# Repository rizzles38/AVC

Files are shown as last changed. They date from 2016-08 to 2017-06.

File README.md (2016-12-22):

# Rover 12

An autonomous 1/10th scale R/C car built by Maria Pikusova and Bob Somers.

## Documentation

### Nodes

* `joint_state_publisher` (joint\_state\_publisher/joint\_state\_publisher):
  Listens on individual joint topics under `/joints` and  publishes a single
  sensor\_msgs/JointState which contains the state of all joints in the robot
  (based on the URDF).
* `robot_state_publisher` (robot\_state\_publisher/state\_publisher): Listens
  to the combined joint states of the robot on `/joint_states`, runs forward
  kinematics based on the URDF, and publishes the results to the TF2 tree.
* `control_board` (rover12\_drivers/control\_board\_node): Driver node which
  talks to the control board. Subscribes to the `/control/autonomous` and
  `/control/command` topics for controlling whether we're in autonomous mode and
  what the velocity/steering command is. Publishes data and status of the wheel
  encoders on the `/wheels/data` and `/wheels/status` topics, as well as the
  status of autonomous mode (from the control board) on `/estop`.
* `sensor_board` (rover12\_drivers/sensor\_board\_node): Publishes data from the
  IMU sensor and GPS sensor, including status information from both sensors
  about their operating modes, current performance, and calibration status.
* `soft_estop` (soft\_estop/soft\_estop): Continuously publishes on the
  `/control/autonomous` topic that requests that the hardware allow the robot to
  be in autonomous mode. Can be run on a computer different than the robot to
  have remote control of autonomous mode. Stands for "software emergency stop".
* `odom_localizer` (robot\_localization/ukf\_localization\_node): Runs an
  unscented Kalman filter over the wheel odometry and IMU data to produce a
  state estimate of `base_link` in the `odom` frame. Subscribes to `/imu/data`
  and `/wheels/data` for sensor inputs and publishes its pose estimate on
  `/odom/filtered`. Also publishes the transform from the `odom` frame to the
  `base_link` frame in the TF2 tree.

### Topics

* `/control`: Namespace for talking to the control board.
  * `/autonomous` (rover12\_drivers/AutonomousMode): Controls whether the
    software wants to be in autonomous mode or not.
  * `/command` (ackermann\_msgs/AckermannDriveStamped): Contains the velocity
    and steering angle command we want the car to execute.
* `/estop` (rover12\_drivers/AutonomousMode): The current state of autonomous
  mode, according to the control board. The firmware makes the final call, based
  on whether the software and physical autonomous mode switch are engaged.
* `/gps`: Namespace for the GPS sensor.
  * `/fix` (sensor\_msgs/NavSatFix): Current GPS position estimate.
  * `/status` (rover12\_drivers/GpsStatus): Extra status information from the
    GPS sensor.
* `/imu`: Namespace for the inertial sensor.
  * `/data` (sensor\_msgs/Imu): Current inertial data and absolute orientation
    estimate from the sensor.
  * `/status` (rover12\_drivers/ImuStatus): Extra status information from the
    IMU, such as its operating mode and calibration state.
* `/joint_states` (sensor\_msgs/JointState): A combined, consistent JointState
  for all joints in the robot, based on the URDF. Published by the
  `joint_state_publisher`.
* `/joints`: Namespace for controlling individual joint states.
  * `/fl_steer` (sensor\_msgs/JointState): Steering rotation of the front left kingpin.
  * `/fr_steer` (sensor\_msgs/JointState): Steering rotation of the front right kingpin.
  * `/fl_wheel` (sensor\_msgs/JointState): Rotation of the front left wheel.
  * `/fr_wheel` (sensor\_msgs/JointState): Rotation of the front right wheel.
  * `/rl_wheel` (sensor\_msgs/JointState): Rotation of the rear left wheel.
  * `/rr_wheel` (sensor\_msgs/JointState): Rotation of the rear right wheel.
* `/odom`: Namespace for pose information in the odom frame.
  * `/filtered` (nav\_msgs/Odometry): Output pose estimate from the UKF in the
    `odom` frame.
* `/wheels`: Namespace for the quadrature wheel encoders.
  * `/data` (geometry\_msgs/TwistWithCovarianceStamped): Instantaneous forward
    speed based on averaging wheel speeds from the quadrature wheel encoders.
  * `/status` (rover12\_drivers/EncoderStatus): Extra status data from the
    wheel encoders (such as raw tick counts).

### TF2 Frames
* `odom`: World-fixed frame in which `base_link` moves smoothly over the short
  term, but accumulates drift error over the long term. The origin of this frame
  is the startup location of the robot.
  * `base_link`: Fixed to robot, parent of all other frames attached to the
    robot. Origin is at the rear axle (X forward, Y out the driver's side, Z
    up).
    * `imu`: Origin at the sensing center of the IMU, oriented according to the
      IMUs local coordinate frame.
    * `gps`: Origen at the sensing center of the GPS antenna, oriented in the
      same direction as `base_link`.
    * `body`: Origin at the approximate center of mass of the body shell,
      primarily used for drawing the robot model at a sensible location in rviz.
    * `rl_wheel`: Origin in the center of the rear left wheel. Rotates about
      its Y axis as the wheel rotates. Located half the track distance from
      `base_link` along its Y axis.
    * `rr_wheel`: Origin in the center of the rear right wheel. Rotates about
      its Y axis as the wheel rotates. Located half the track distance from
      `base_link` along its Y axis.
    * `f_axle`: Origin in the center of the front axle, oriented in the same
      way as `base_link`. The distance between this frame and `base_link` is the
      wheelbase distance along their colinear X axes.
      * `fl_kingpin`: Origin in the steering center of the front left wheel,
        located half the track distance from `f_axle` along its Y axis. Rotates
        about its Z axis.
        * `fl_wheel`: Origin in the center of the front left wheel, orientation
          accounting for the rotation of `fl_kingpin`. Rotates about its Y axis
          as the wheel rotates.
      * `fr_kingpin`: Origin in the steering center of the front right wheel,
        located half the track distance from `f_axle` along its Y axis. Rotates
        about its Z axis.
        * `fr_wheel`: Origin in the center of the front right wheel, orientation
          accounting for the rotation of `fr_kingpin`. Rotates about its Y axis
          as the wheel rotates.

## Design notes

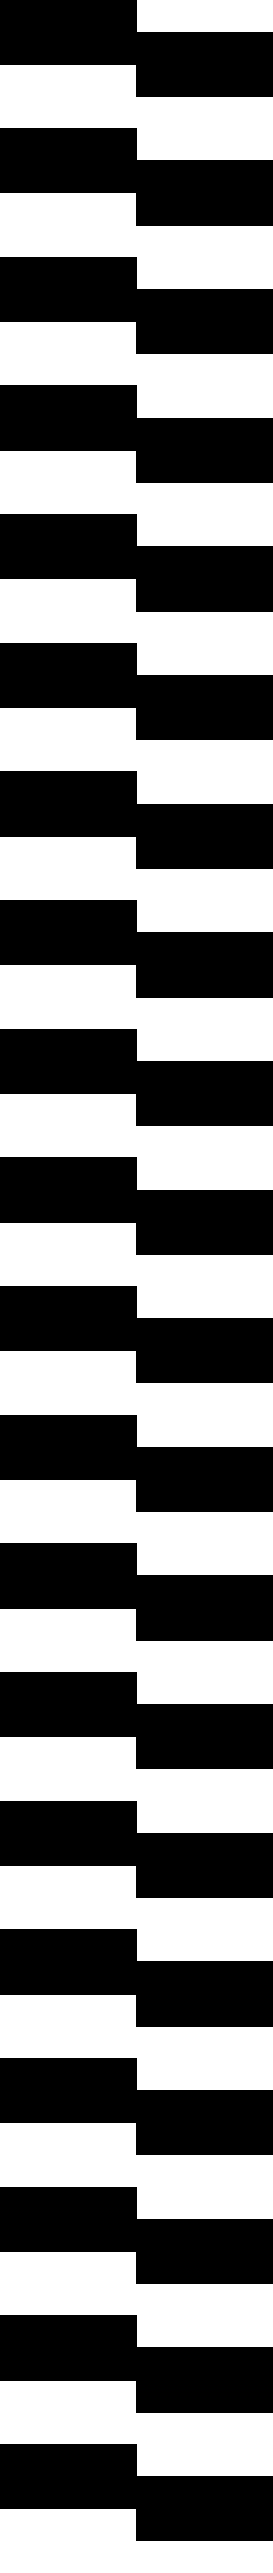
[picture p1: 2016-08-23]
tools/quadrature_patterns/pattern.png

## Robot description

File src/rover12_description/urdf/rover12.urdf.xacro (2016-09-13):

<?xml version="1.0"?>
<robot xmlns:xacro="http://www.ros.org/wiki/xacro" name="rover12">
  <xacro:property name="PI" value="3.1415926535897931"/>

  <xacro:property name="r_track" value="0.2667"/>
  <xacro:property name="f_track" value="0.257175"/>
  <xacro:property name="wheelbase" value="0.32385"/>

  <xacro:property name="wheel_width" value="0.0508"/>
  <xacro:property name="wheel_radius" value="0.0492125"/>

  <xacro:property name="gps_xyz" value="0.375 0 0.03"/>
  <xacro:property name="gps_rpy" value="0 0 0"/>

  <xacro:property name="imu_xyz" value="0.28 0.038 0.072"/>
  <xacro:property name="imu_rpy" value="0 0.0349066 1.55334"/>

  <material name="axle">
    <color rgba="1.0 1.0 1.0 1.0"/>
  </material>

  <xacro:macro name="axle" params="name track wheelbase">
    <link name="${name}">
      <visual>
        <geometry>
          <cylinder length="${track}" radius="0.00635"/>
        </geometry>
        <material name="axle"/>
        <origin rpy="${PI /2 } 0 0"/>
      </visual>
    </link>

    <joint name="base_link_to_${name}" type="fixed">
      <parent link="base_link"/>
      <child link="${name}"/>
      <origin xyz="${wheelbase} 0 0"/>
    </joint>
  </xacro:macro>

  <xacro:macro name="wheel" params="name reflect">
    <link name="${name}">
      <visual>
        <geometry>
          <mesh filename="package://rover12_description/meshes/wheel.dae" scale="0.5 ${reflect * 0.8} 0.5"/>
        </geometry>
      </visual>
    </link>
  </xacro:macro>

  <xacro:macro name="fixed_wheel" params="name axle track reflect">
    <xacro:wheel name="${name}_wheel" reflect="${reflect}"/>

    <joint name="${axle}_to_${name}_wheel" type="continuous">
      <parent link="${axle}"/>
      <child link="${name}_wheel"/>
      <axis xyz="0 1 0"/>
      <origin xyz="0 ${reflect * track / 2} 0"/>
    </joint>
  </xacro:macro>

  <xacro:macro name="steerable_wheel" params="name axle track reflect">
    <link name="${name}_kingpin"/>

    <joint name="${axle}_to_${name}_kingpin" type="continuous">
      <parent link="${axle}"/>
      <child link="${name}_kingpin"/>
      <axis xyz="0 0 1"/>
      <origin xyz="0 ${reflect * track / 2} 0"/>
    </joint>

    <xacro:fixed_wheel name="${name}" axle="${name}_kingpin" track="0" reflect="${reflect}"/>
  </xacro:macro>

  <link name="base_link">
    <visual>
      <geometry>
        <cylinder length="${r_track}" radius="0.00635"/>
      </geometry>
      <material name="axle"/>
      <origin rpy="${PI / 2} 0 0"/>
    </visual>
  </link>

  <xacro:fixed_wheel name="rl" axle="base_link" track="${r_track}" reflect="1"/>
  <xacro:fixed_wheel name="rr" axle="base_link" track="${r_track}" reflect="-1"/>

  <xacro:axle name="f_axle" track="${f_track}" wheelbase="${wheelbase}"/>

  <xacro:steerable_wheel name="fl" axle="f_axle" track="${f_track}" reflect="1"/>
  <xacro:steerable_wheel name="fr" axle="f_axle" track="${f_track}" reflect="-1"/>

  <link name="gps"/>

  <joint name="base_link_to_gps" type="fixed">
    <parent link="base_link"/>
    <child link="gps"/>
    <origin xyz="${gps_xyz}" rpy="${gps_rpy}"/>
  </joint>

  <link name="imu"/>

  <joint name="base_link_to_imu" type="fixed">
    <parent link="base_link"/>
    <child link="imu"/>
    <origin xyz="${imu_xyz}" rpy="${imu_rpy}"/>
  </joint>

  <link name="body">
    <visual>
      <geometry>
        <mesh filename="package://rover12_description/meshes/body.dae" scale="-0.48 0.5 0.5"/>
      </geometry>
    </visual>
  </link>

  <joint name="base_link_to_body" type="fixed">
    <parent link="base_link"/>
    <child link="body"/>
    <origin xyz="0.175 0 0.067"/>
  </joint>
</robot>

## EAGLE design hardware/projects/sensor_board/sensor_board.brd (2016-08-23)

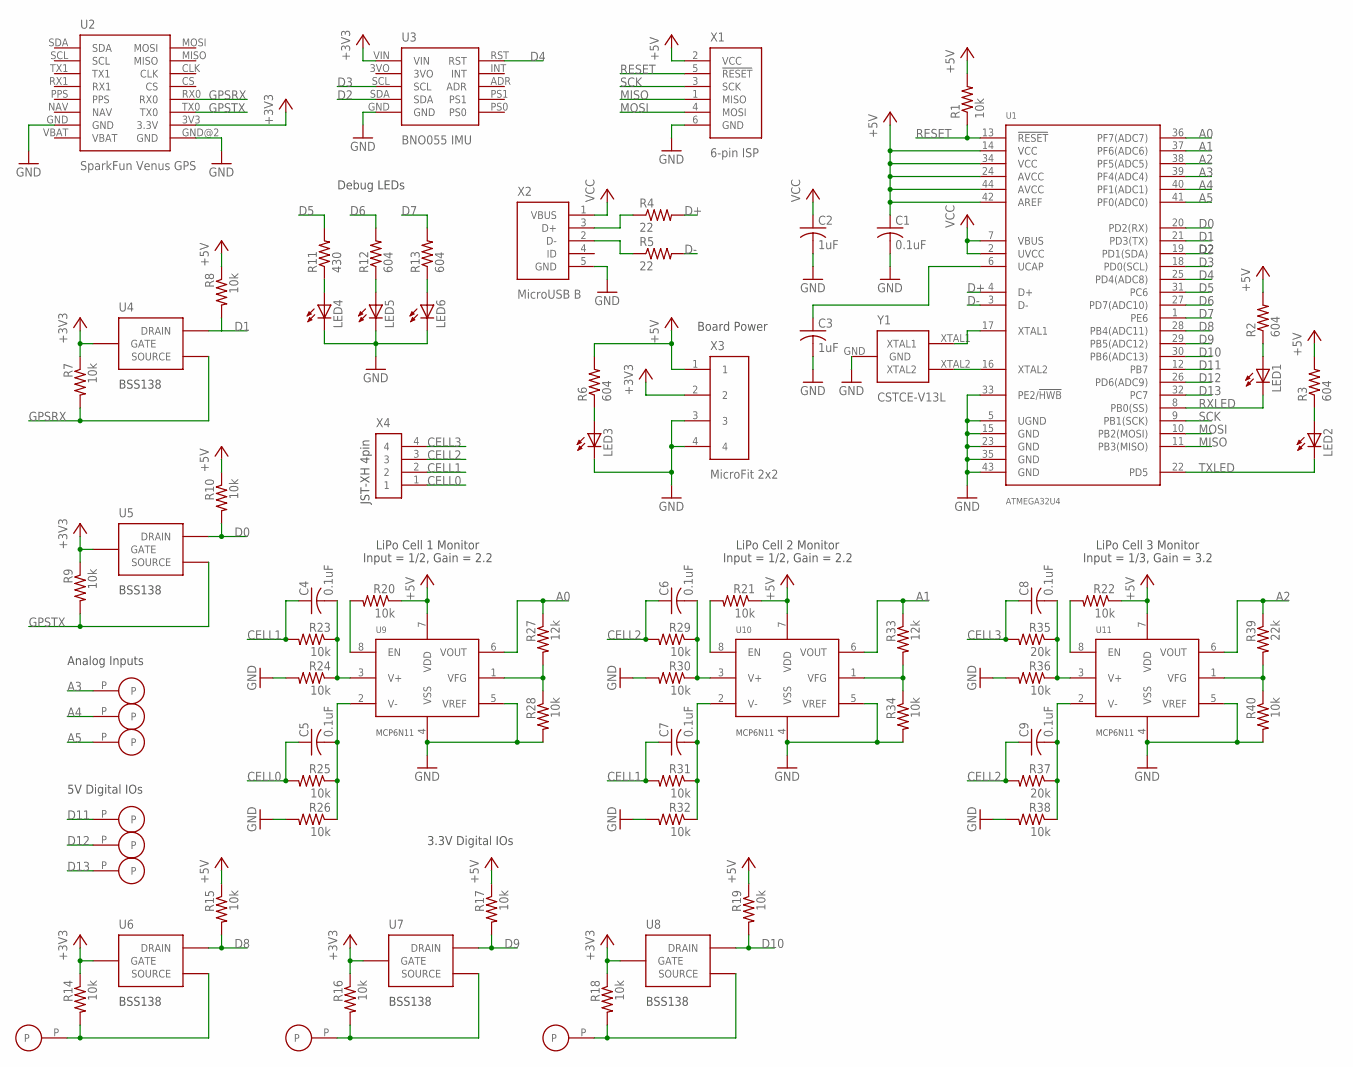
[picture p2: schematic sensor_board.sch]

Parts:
C1, C4, C5, C6, C7, C8, C9: 0.1uF; C0603
C2, C3: 1uF; C0603
LED1, LED2, LED3, LED4, LED5, LED6: LEDCHIPLED_0603; CHIPLED_0603
P1, P2, P3, P4, P5, P6, P8, P9, P10: 100MIL-PAD
R1, R7, R8, R9, R10, R14, R15, R16, R17, R18, R19, R20, R21, R22, R23, R24, R25, R26, R28, R29, R30, R31, R32, R34, R36, R38, R40: 10k; R0603
R2, R3, R6, R12, R13: 604; R0603
R4, R5: 22; R0603
R11: 430; R0603
R27, R33: 12k; R0603
R35, R37: 20k; R0603
R39: 22k; R0603
U1: ATMEGA32U4; TQFP-44
U2: SPARKFUN-VENUS-GPS
U3: ADAFRUIT-BNO055-IMU
U4, U5, U6, U7, U8: BSS138; SOT-23
U9, U10, U11: MCP6N11; SOIC-8
X1: ISP-HEADER
X2: MICRO-USB-B
X3: MICROFIT-2X2-SMD; MICROFIT-2X2-0430450411
X4: JST-XH-4
Y1: CSTCE-V13L

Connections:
3V3D8: P4.P, R14.2, U6.SOURCE
3V3D9: P5.P, R16.2, U7.SOURCE
3V3D10: P6.P, R18.2, U8.SOURCE
3VO: U3.3VO
+3V3: R7.1, R9.1, R14.1, R16.1, R18.1, U2.3V3 (3.3V), U3.VIN, U4.GATE, U5.GATE, U6.GATE, U7.GATE, U8.GATE, X3.2
+5V: C1.1, R1.2, R2.2, R3.2, R6.2, R8.1, R10.1, R15.1, R17.1, R19.1, R20.1, R21.1, R22.1, U1.14 (VCC), U1.24 (AVCC), U1.34 (VCC), U1.42 (AREF), U1.44 (AVCC), U9.7 (VDD), U10.7 (VDD), U11.7 (VDD), X1.2 (VCC), X3.1
A0: R27.1, U1.36 (PF7(ADC7)), U9.6 (VOUT)
A1: R33.1, U1.37 (PF6(ADC6)), U10.6 (VOUT)
A2: R39.1, U1.38 (PF5(ADC5)), U11.6 (VOUT)
A3: P8.P, U1.39 (PF4(ADC4))
A4: P9.P, U1.40 (PF1(ADC1))
A5: P10.P, U1.41 (PF0(ADC0))
CELL0: C5.1, R25.2, X4.1
CELL1: C4.1, C7.1, R23.2, R31.2, X4.2
CELL2: C6.1, C9.1, R29.2, R37.2, X4.3
CELL3: C8.1, R35.2, X4.4
D0: R10.2, U1.20 (PD2(RX)), U5.DRAIN
D1: R8.2, U1.21 (PD3(TX)), U4.DRAIN
D2: U1.19 (PD1(SDA)), U3.SDA
D3: U1.18 (PD0(SCL)), U3.SCL
D4: U1.25 (PD4(ADC8)), U3.RST
D5: R11.2, U1.31 (PC6)
D6: R12.2, U1.27 (PD7(ADC10))
D7: R13.2, U1.1 (PE6)
D8: R15.2, U1.28 (PB4(ADC11)), U6.DRAIN
D9: R17.2, U1.29 (PB5(ADC12)), U7.DRAIN
D10: R19.2, U1.30 (PB6(ADC13)), U8.DRAIN
D11: P1.P, U1.12 (PB7)
D12: P2.P, U1.26 (PD6(ADC9))
D13: P3.P, U1.32 (PC7)
D+: R4.2, U1.4 (D+)
D-: R5.2, U1.3 (D-)
GND: C1.2, C2.2, C3.2, LED3.C, LED4.C, LED5.C, LED6.C, R24.2, R26.2, R28.2, R30.2, R32.2, R34.2, R36.2, R38.2, R40.2, U1.5 (UGND), U1.15 (GND), U1.23 (GND), U1.33 (PE2/!HWB!), U1.35 (GND), U1.43 (GND), U2.GND, U2.GND@2 (GND), U3.GND, U9.4 (VSS), U9.5 (VREF), U10.4 (VSS), U10.5 (VREF), U11.4 (VSS), U11.5 (VREF), X1.6 (GND), X2.5 (GND), X3.3, X3.4, Y1.GND
GPSRX: R7.2, U2.RX0, U4.SOURCE
GPSTX: R9.2, U2.TX0, U5.SOURCE
MISO: U1.11 (PB3(MISO)), X1.1 (MISO)
MOSI: U1.10 (PB2(MOSI)), X1.4 (MOSI)
unnamed: LED3.A, R6.1
unnamed: C3.1, U1.6 (UCAP)
unnamed: LED1.A, R2.1
unnamed: LED2.A, R3.1
unnamed: U1.16 (XTAL2), Y1.XTAL2
unnamed: U1.17 (XTAL1), Y1.XTAL1
unnamed: R20.2, U9.8 (EN)
unnamed: R5.1, X2.2 (D-)
unnamed: R4.1, X2.3 (D+)
unnamed: LED4.A, R11.1
unnamed: LED5.A, R12.1
unnamed: LED6.A, R13.1
unnamed: R21.2, U10.8 (EN)
unnamed: R22.2, U11.8 (EN)
unnamed: C4.2, R23.1, R24.1, U9.3 (V+)
unnamed: C8.2, R35.1, R36.1, U11.3 (V+)
unnamed: C5.2, R25.1, R26.1, U9.2 (V-)
unnamed: C6.2, R29.1, R30.1, U10.3 (V+)
unnamed: R27.2, R28.1, U9.1 (VFG)
unnamed: C7.2, R31.1, R32.1, U10.2 (V-)
unnamed: C9.2, R37.1, R38.1, U11.2 (V-)
unnamed: R33.2, R34.1, U10.1 (VFG)
unnamed: R39.2, R40.1, U11.1 (VFG)
RESET: R1.1, U1.13 (!RESET!), X1.5 (!RESET!)
RXLED: LED1.C, U1.8 (PB0(SS))
SCK: U1.9 (PB1(SCK)), X1.3 (SCK)
TXLED: LED2.C, U1.22 (PD5)
VBAT: U2.VBAT
VCC: C2.1, U1.2 (UVCC), U1.7 (VBUS), X2.1 (VBUS)

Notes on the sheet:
Board Power
Debug LEDs
3.3V Digital IOs
5V Digital IOs
Analog Inputs
LiPo Cell 1 Monitor
LiPo Cell 2 Monitor
LiPo Cell 3 Monitor
Input = 1/2, Gain = 2.2
Input = 1/3, Gain = 3.2

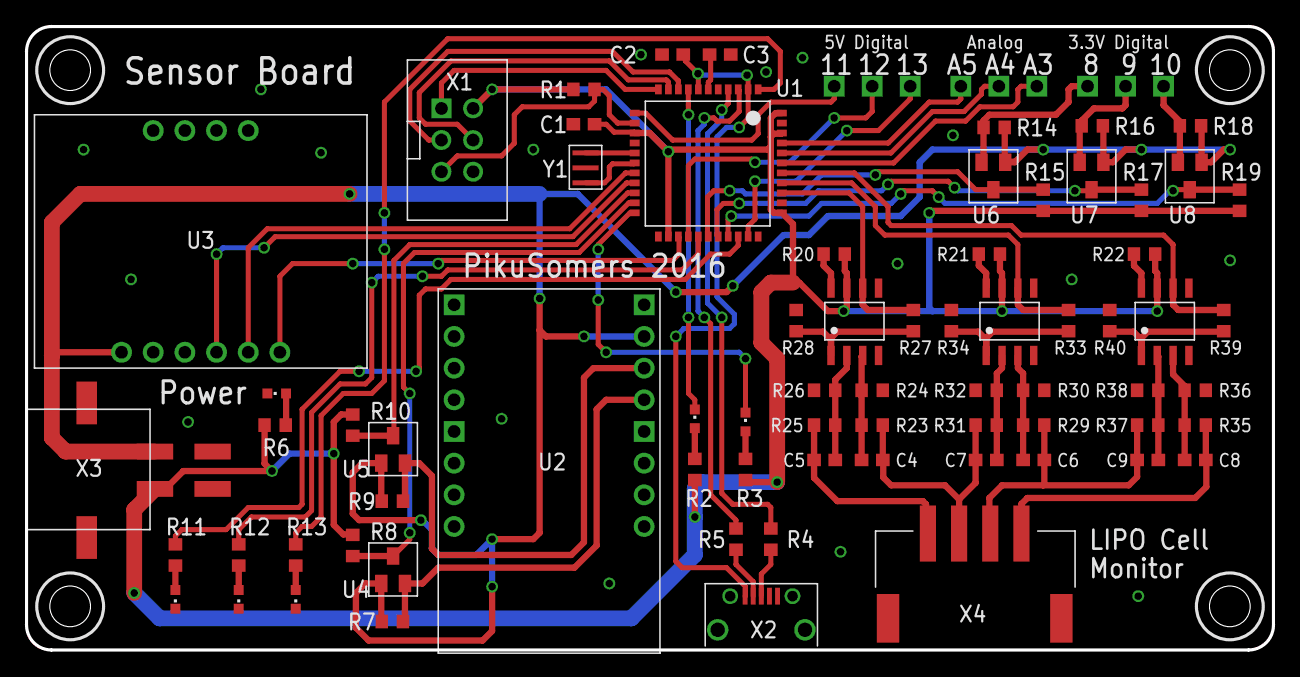
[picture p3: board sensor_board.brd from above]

Board: 2 copper layers, 100.0 x 50.0 mm, 80 parts (0 on the bottom side), 64 nets.

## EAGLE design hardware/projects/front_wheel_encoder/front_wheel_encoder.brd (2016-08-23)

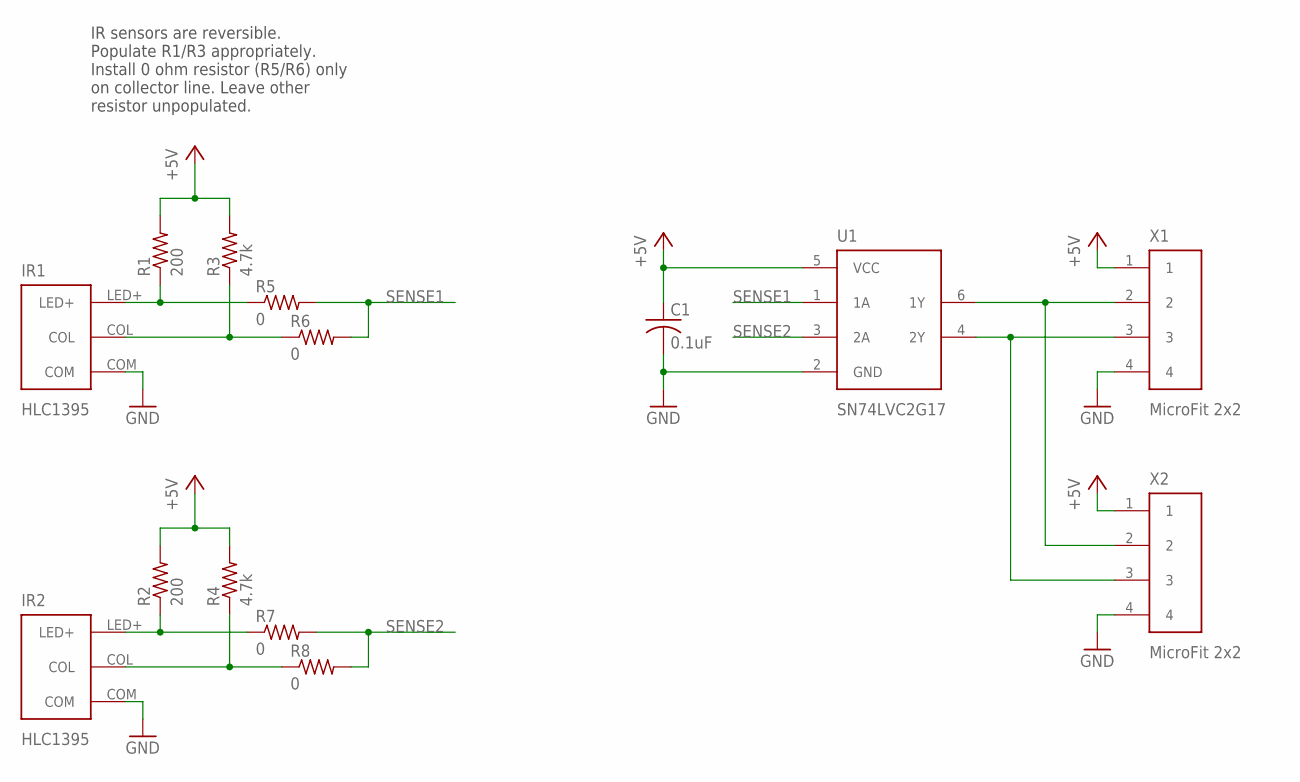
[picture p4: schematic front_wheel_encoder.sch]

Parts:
C1: 0.1uF; C0603
IR1, IR2: HLC1395
R1, R2: 200; R0603
R3, R4: 4.7k; R0603
R5, R6, R7, R8: 0; R0603
U1: SN74LVC2G17DBVR; SOT-23-6
X1, X2: MICROFIT-2X2-SMD; MICROFIT-2X2-0430450411

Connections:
+5V: C1.1, R1.2, R2.2, R3.2, R4.2, U1.5 (VCC), X1.1, X2.1
GND: C1.2, IR1.COM, IR2.COM, U1.2 (GND), X1.4, X2.4
unnamed: IR1.LED+, R1.1, R5.1
unnamed: IR2.LED+, R2.1, R7.1
unnamed: IR2.COL, R4.1, R8.1
unnamed: U1.4 (2Y), X1.3, X2.3
unnamed: U1.6 (1Y), X1.2, X2.2
unnamed: IR1.COL, R3.1, R6.1
SENSE1: R5.2, R6.2, U1.1 (1A)
SENSE2: R7.2, R8.2, U1.3 (2A)

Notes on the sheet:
IR sensors are reversible. Populate R1/R3 appropriately. Install 0 ohm resistor (R5/R6) only on collector line. Leave other resistor unpopulated.

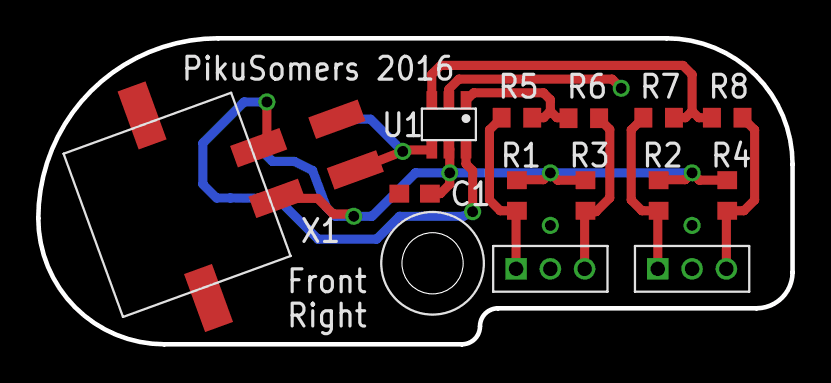
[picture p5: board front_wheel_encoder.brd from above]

Board: 2 copper layers, 41.9 x 17.0 mm, 14 parts (1 on the bottom side), 10 nets.

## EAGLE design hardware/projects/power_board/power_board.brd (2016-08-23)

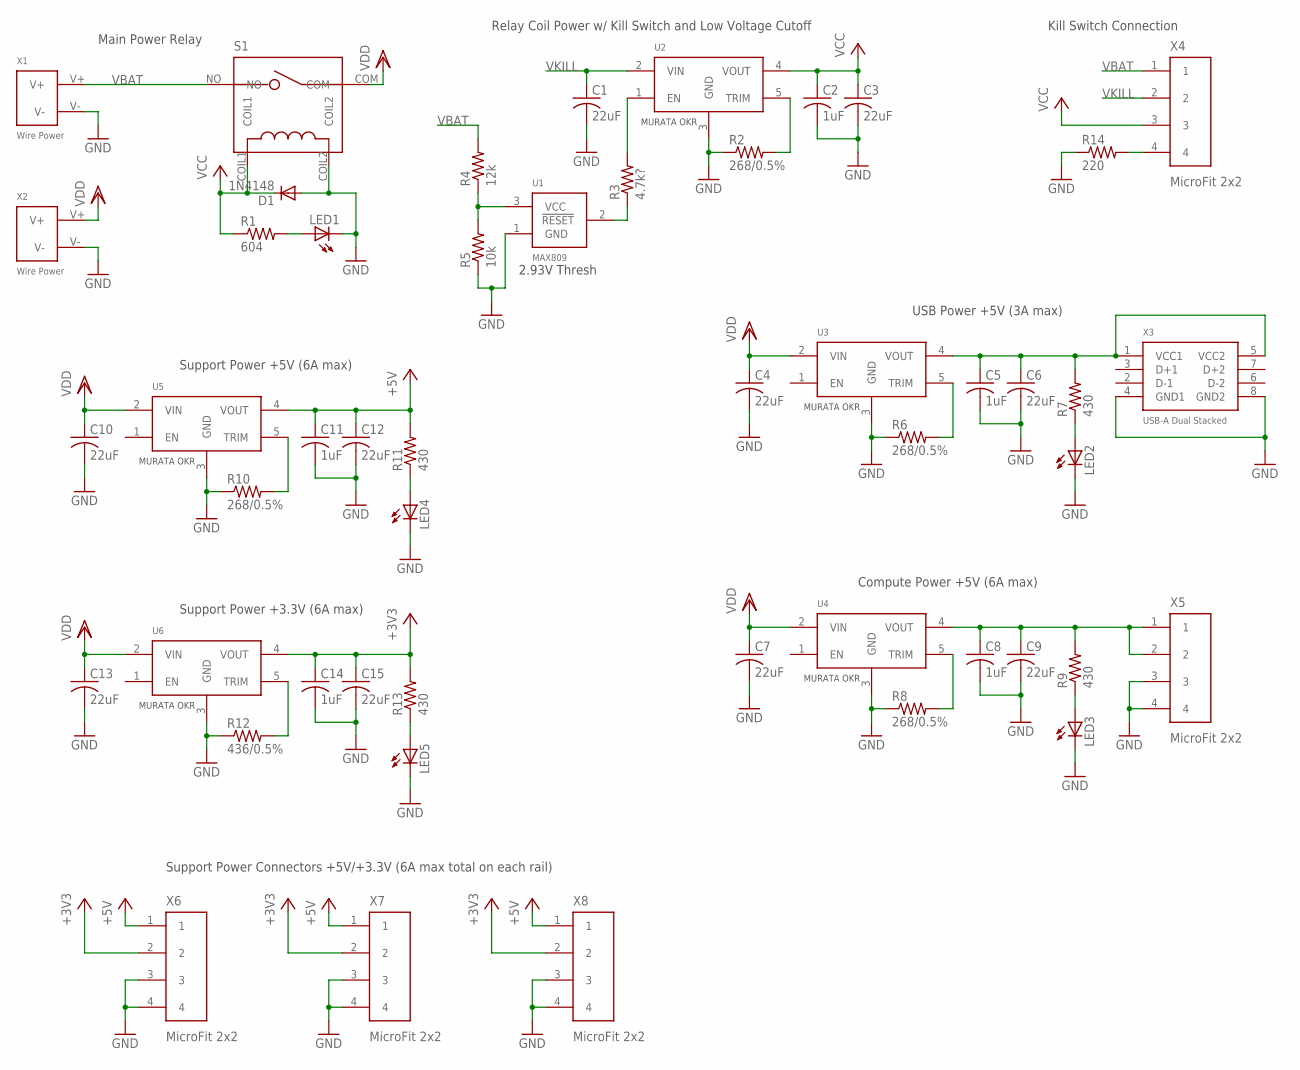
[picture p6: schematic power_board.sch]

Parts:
C1, C3, C4, C6, C7, C9, C10, C12, C13, C15: 22uF; C1210
C2, C5, C8, C11, C14: 1uF; C1210
D1: 1N4148; SOD123
LED1, LED2, LED3, LED4, LED5: LEDCHIPLED_0603; CHIPLED_0603
R1: 604; R0603
R2, R6, R8, R10: 268/0.5%; R0603
R3: 4.7k?; R0603
R4: 12k; R0603
R5: 10k; R0603
R7, R9, R11, R13: 430; R0603
R12: 436/0.5%; R0603
R14: 220; R0603
S1: T90S1D12-5
U1: MAX809; SOT-23
U2, U3, U4, U5, U6: MURATA-OKR
X1, X2: WIRE-POWER
X3: USB-A-STACKED
X4, X5, X6, X7, X8: MICROFIT-2X2-SMD; MICROFIT-2X2-0430450411

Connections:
+3V3: C14.1, C15.1, R13.2, U6.4 (VOUT), X6.2, X7.2, X8.2
+5V: C11.1, C12.1, R11.2, U5.4 (VOUT), X6.1, X7.1, X8.1
GND: C1.2, C2.2, C3.2, C4.2, C5.2, C6.2, C7.2, C8.2, C9.2, C10.2, C11.2, C12.2, C13.2, C14.2, C15.2, D1.A, LED1.C, LED2.C, LED3.C, LED4.C, LED5.C, R2.1, R5.1, R6.1, R8.1, R10.1, R12.1, R14.1, S1.COIL2, U1.1 (GND), U2.3 (GND), U3.3 (GND), U4.3 (GND), U5.3 (GND), U6.3 (GND), X1.V-, X2.V-, X3.4 (GND1), X3.8 (GND2), X5.3, X5.4, X6.3, X6.4, X7.3, X7.4, X8.3, X8.4
unnamed: LED2.A, R7.1
unnamed: LED1.A, R1.2
unnamed: R2.2, U2.5 (TRIM)
unnamed: R3.1, U1.2 (!RESET!)
unnamed: R8.2, U4.5 (TRIM)
unnamed: R6.2, U3.5 (TRIM)
unnamed: R4.1, R5.2, U1.3 (VCC)
unnamed: C8.1, C9.1, R9.2, U4.4 (VOUT), X5.1, X5.2
unnamed: LED3.A, R9.1
unnamed: LED4.A, R11.1
unnamed: LED5.A, R13.1
unnamed: R3.2, U2.1 (EN)
unnamed: R12.2, U6.5 (TRIM)
unnamed: R10.2, U5.5 (TRIM)
unnamed: R14.2, X4.4
USB5V: C5.1, C6.1, R7.2, U3.4 (VOUT), X3.1 (VCC1), X3.5 (VCC2)
VBAT: R4.2, S1.NO, X1.V+, X4.1
VCC: C2.1, C3.1, D1.C, R1.1, S1.COIL1, U2.4 (VOUT), X4.3
VDD: C4.1, C7.1, C10.1, C13.1, S1.COM, U3.2 (VIN), U4.2 (VIN), U5.2 (VIN), U6.2 (VIN), X2.V+
VKILL: C1.1, U2.2 (VIN), X4.2

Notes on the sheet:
Main Power Relay
Relay Coil Power w/ Kill Switch and Low Voltage Cutoff
Kill Switch Connection
USB Power +5V (3A max)
Compute Power +5V (6A max)
Support Power +5V (6A max)
Support Power +3.3V (6A max)
Support Power Connectors +5V/+3.3V (6A max total on each rail)
2.93V Thresh

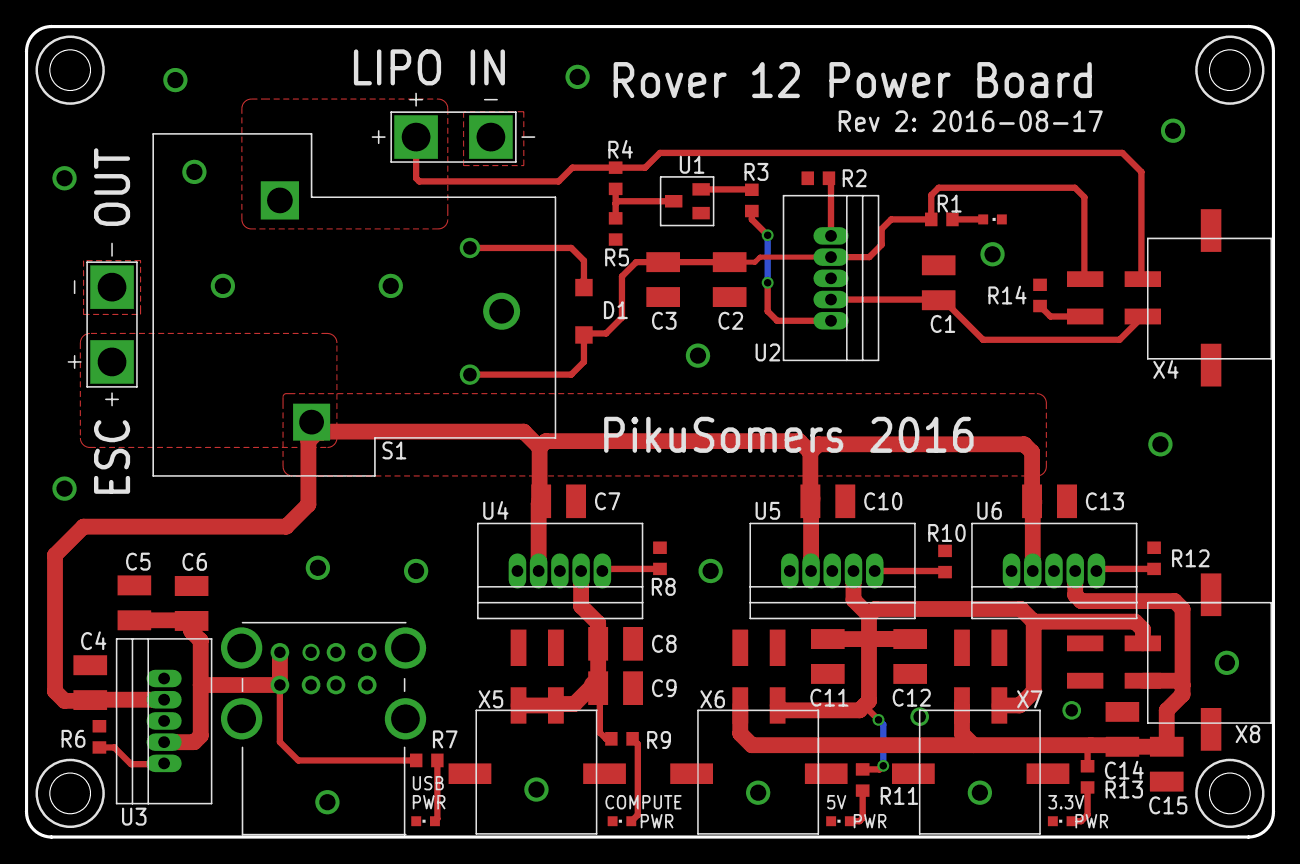
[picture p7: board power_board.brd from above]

Board: 2 copper layers, 100.0 x 65.0 mm, 50 parts (0 on the bottom side), 23 nets.

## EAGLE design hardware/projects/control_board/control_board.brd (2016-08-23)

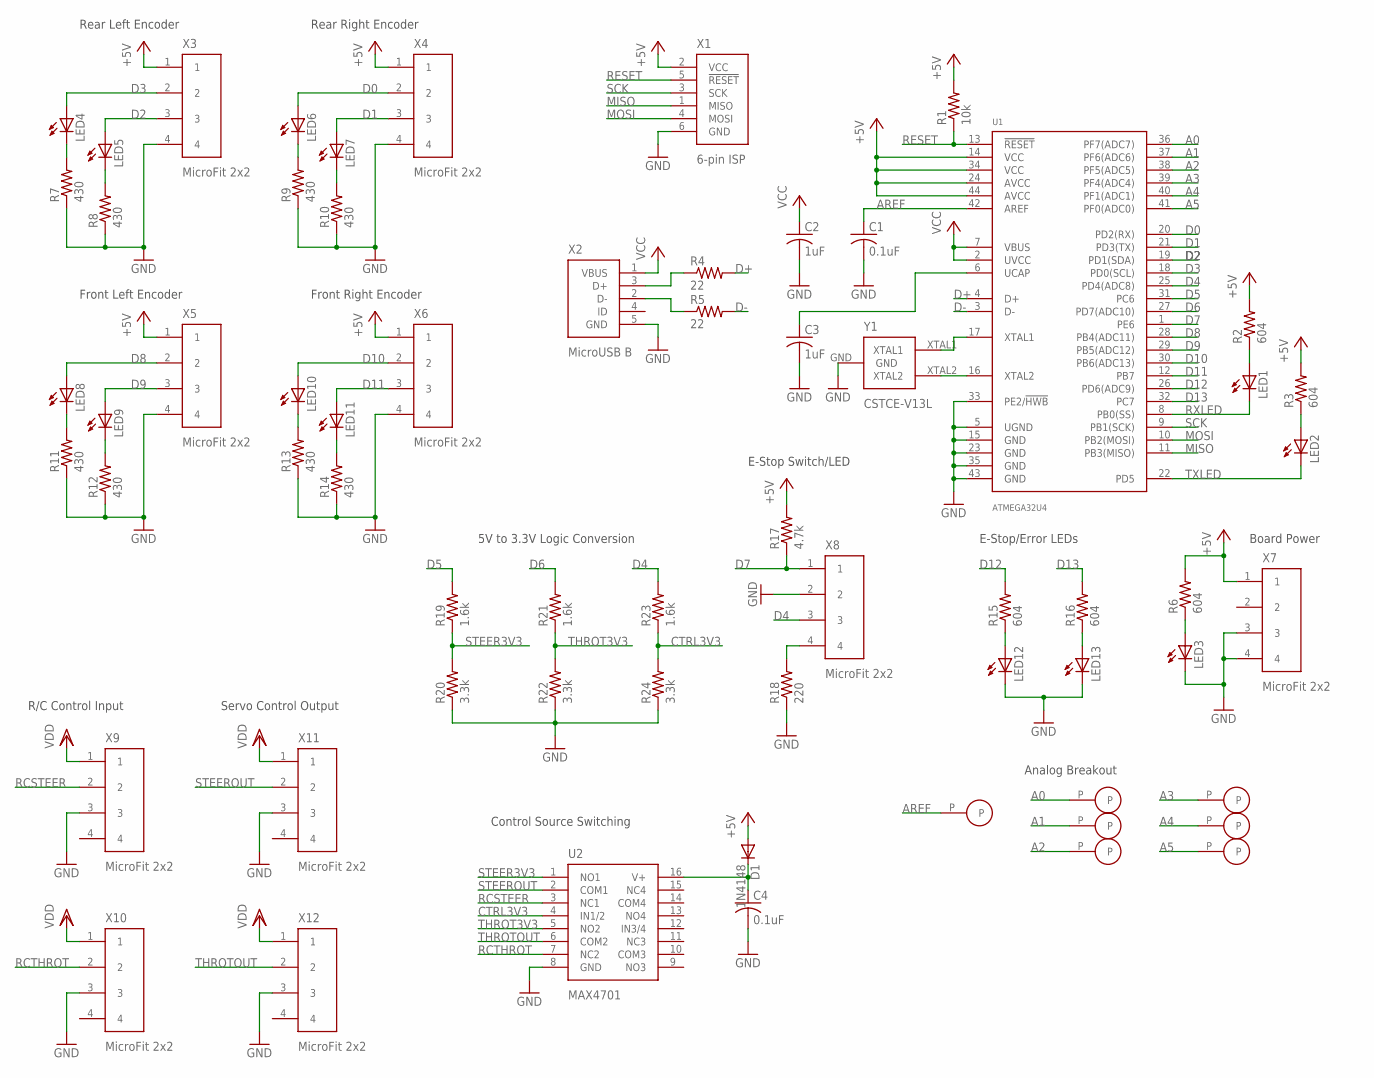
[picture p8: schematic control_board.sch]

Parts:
C1, C4: 0.1uF; C0603
C2, C3: 1uF; C0603
D1: 1N4148; SOD123
LED1, LED2, LED3, LED4, LED5, LED6, LED7, LED8, LED9, LED10, LED11, LED12, LED13: LEDCHIPLED_0603; CHIPLED_0603
P1, P2, P3, P4, P5, P6, P7: 100MIL-PAD
R1: 10k; R0603
R2, R3, R6, R15, R16: 604; R0603
R4, R5: 22; R0603
R7, R8, R9, R10, R11, R12, R13, R14: 430; R0603
R17: 4.7k; R0603
R18: 220; R0603
R19, R21, R23: 1.6k; R0603
R20, R22, R24: 3.3k; R0603
U1: ATMEGA32U4; TQFP-44
U2: MAX4701; TSSOP-16
X1: ISP-HEADER
X2: MICRO-USB-B
X3, X4, X5, X6, X7, X8, X9, X10, X11, X12: MICROFIT-2X2-SMD; MICROFIT-2X2-0430450411
Y1: CSTCE-V13L

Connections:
+5V: D1.A, R1.2, R2.2, R3.2, R6.2, R17.2, U1.14 (VCC), U1.24 (AVCC), U1.34 (VCC), U1.44 (AVCC), X1.2 (VCC), X3.1, X4.1, X5.1, X6.1, X7.1
A0: P2.P, U1.36 (PF7(ADC7))
A1: P3.P, U1.37 (PF6(ADC6))
A2: P4.P, U1.38 (PF5(ADC5))
A3: P5.P, U1.39 (PF4(ADC4))
A4: P6.P, U1.40 (PF1(ADC1))
A5: P7.P, U1.41 (PF0(ADC0))
AREF: C1.1, P1.P, U1.42 (AREF)
CTRL3V3: R23.1, R24.2, U2.4 (IN1/2)
D0: LED6.A, U1.20 (PD2(RX)), X4.2
D1: LED7.A, U1.21 (PD3(TX)), X4.3
D2: LED5.A, U1.19 (PD1(SDA)), X3.3
D3: LED4.A, U1.18 (PD0(SCL)), X3.2
D4: R23.2, U1.25 (PD4(ADC8)), X8.3
D5: R19.2, U1.31 (PC6)
D6: R21.2, U1.27 (PD7(ADC10))
D7: R17.1, U1.1 (PE6), X8.1
D8: LED8.A, U1.28 (PB4(ADC11)), X5.2
D9: LED9.A, U1.29 (PB5(ADC12)), X5.3
D10: LED10.A, U1.30 (PB6(ADC13)), X6.2
D11: LED11.A, U1.12 (PB7), X6.3
D12: R15.2, U1.26 (PD6(ADC9))
D13: R16.2, U1.32 (PC7)
D+: R4.2, U1.4 (D+)
D-: R5.2, U1.3 (D-)
GND: C1.2, C2.2, C3.2, C4.2, LED3.C, LED12.C, LED13.C, R7.1, R8.1, R9.1, R10.1, R11.1, R12.1, R13.1, R14.1, R18.1, R20.1, R22.1, R24.1, U1.5 (UGND), U1.15 (GND), U1.23 (GND), U1.33 (PE2/!HWB!), U1.35 (GND), U1.43 (GND), U2.8 (GND), X1.6 (GND), X2.5 (GND), X3.4, X4.4, X5.4, X6.4, X7.3, X7.4, X8.2, X9.3, X10.3, X11.3, X12.3, Y1.GND
MISO: U1.11 (PB3(MISO)), X1.1 (MISO)
MOSI: U1.10 (PB2(MOSI)), X1.4 (MOSI)
unnamed: LED3.A, R6.1
unnamed: C3.1, U1.6 (UCAP)
unnamed: LED1.A, R2.1
unnamed: LED2.A, R3.1
unnamed: U1.16 (XTAL2), Y1.XTAL2
unnamed: U1.17 (XTAL1), Y1.XTAL1
unnamed: LED7.C, R10.2
unnamed: R5.1, X2.2 (D-)
unnamed: R4.1, X2.3 (D+)
unnamed: LED4.C, R7.2
unnamed: LED6.C, R9.2
unnamed: LED5.C, R8.2
unnamed: LED8.C, R11.2
unnamed: LED9.C, R12.2
unnamed: LED12.A, R15.1
unnamed: LED13.A, R16.1
unnamed: R18.2, X8.4
unnamed: LED10.C, R13.2
unnamed: LED11.C, R14.2
unnamed: C4.1, D1.C, U2.16 (V+)
RCSTEER: U2.3 (NC1), X9.2
RCTHROT: U2.7 (NC2), X10.2
RESET: R1.1, U1.13 (!RESET!), X1.5 (!RESET!)
RXLED: LED1.C, U1.8 (PB0(SS))
SCK: U1.9 (PB1(SCK)), X1.3 (SCK)
STEER3V3: R19.1, R20.2, U2.1 (NO1)
STEEROUT: U2.2 (COM1), X11.2
THROT3V3: R21.1, R22.2, U2.5 (NO2)
THROTOUT: U2.6 (COM2), X12.2
TXLED: LED2.C, U1.22 (PD5)
VCC: C2.1, U1.2 (UVCC), U1.7 (VBUS), X2.1 (VBUS)
VDD: X9.1, X10.1, X11.1, X12.1

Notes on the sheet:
Rear Left Encoder
Rear Right Encoder
Front Left Encoder
Front Right Encoder
Board Power
E-Stop/Error LEDs
E-Stop Switch/LED
R/C Control Input
Servo Control Output
Control Source Switching
5V to 3.3V Logic Conversion
Analog Breakout

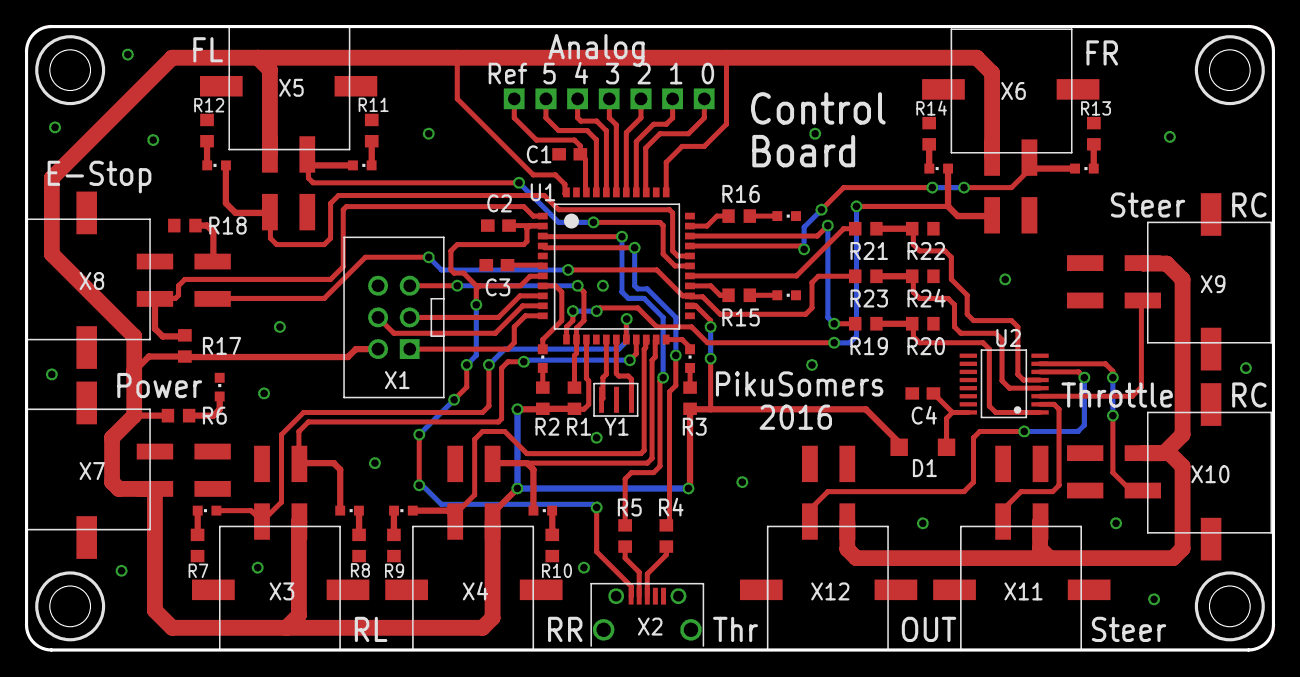
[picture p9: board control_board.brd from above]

Board: 2 copper layers, 100.0 x 50.0 mm, 64 parts (0 on the bottom side), 60 nets.

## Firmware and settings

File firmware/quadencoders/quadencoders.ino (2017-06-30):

#include <stdint.h>
#include <string.h>

#include <FastGPIO.h>
#include <Servo.h>
#include <rover12_comm.h>

#define RR_B 0
#define RR_A 1
#define RL_B 2
#define RL_A 3
#define FR_A 10
#define FR_B 11
#define FL_A 8
#define FL_B 9
#define ORANGE_LED 12
#define RED_LED 13
#define ESTOP_IN 7
#define AUTONOMOUS_OUT 4
#define STEER_OUT 5
#define THROT_OUT 6

#define COMP_BAUD_RATE 115200

void orangeLED(int value) {
  FastGPIO::Pin<ORANGE_LED>::setOutput(value);
}

void redLED(int value) {
  FastGPIO::Pin<RED_LED>::setOutput(value);
}

void debugMsg(const char* s) {
  rover12_comm::DebugMsg debug_msg;
  debug_msg.data.setName(s);
  debug_msg.encode();
  Serial.write(reinterpret_cast<uint8_t*>(&debug_msg), sizeof(debug_msg));
}

void debugInt(const char* name, int32_t i) {
  rover12_comm::DebugMsg debug_msg;
  debug_msg.data.setInt(name, i);
  debug_msg.encode();
  Serial.write(reinterpret_cast<uint8_t*>(&debug_msg), sizeof(debug_msg));
}

void debugFloat(const char* name, float f) {
  rover12_comm::DebugMsg debug_msg;
  debug_msg.data.setFloat(name, f);
  debug_msg.encode();
  Serial.write(reinterpret_cast<uint8_t*>(&debug_msg), sizeof(debug_msg));
}

class WheelEncoders {
public:
  explicit WheelEncoders(int interval) :
    count_rear_left_(0),
    count_rear_right_(0),
    next_time_(0),
    interval_(interval) {}

  void incrementRearLeft() { ++count_rear_left_; }
  void decrementRearLeft() { --count_rear_left_; }
  void incrementRearRight() { ++count_rear_right_; }
  void decrementRearRight() { --count_rear_right_; }

  // 10Hz
  void process() {
    unsigned long now = millis();
    if (next_time_ == 0) {
      next_time_ = now + interval_;
      return;
    } else if (now >= next_time_) {
      // Set the next sample time.
      next_time_ = now + interval_;

      // Create a message
      rover12_comm::WheelEncMsg wheel_enc_msg;

      // Populate each wheel encoder count
      wheel_enc_msg.data.count_rear_left = count_rear_left_;
      wheel_enc_msg.data.count_rear_right = count_rear_right_;

      // Timestamp the message in hardware.
      wheel_enc_msg.data.hw_timestamp_ms = millis();

      // Encode and write to Serial
      wheel_enc_msg.encode();
      Serial.write(reinterpret_cast<uint8_t*>(&wheel_enc_msg), sizeof(wheel_enc_msg));
    }
  }

private:
  volatile int32_t count_rear_left_;
  volatile int32_t count_rear_right_;
  unsigned long next_time_;
  int interval_;
};

class Messenger {
public:
  explicit Messenger()
    : buffer_idx_(-1),
      steering_us_(1556),
      throttle_us_(1500),
      estop_(false),
      last_estop_time_(0),
      next_time_(0) {
    memset(buf_, 0, sizeof(buf_));
  }

  // Getters for data managed by the messenger.
  int steering_us() const { return steering_us_; }
  int throttle_us() const { return throttle_us_; }
  bool estop() const { return estop_; }
  unsigned long last_estop_time() const { return last_estop_time_; }

  void setup() {
    while (!Serial); // Wait for USB serial connection to open.
    Serial.begin(COMP_BAUD_RATE);
  }

  void process(bool autonomous_mode) {
    // Read bytes from the serial port into our buffer.
    while (Serial.available() > 0) {
      int b = Serial.read();
      if (buffer_idx_ < 0) {
        // Not synced yet.
        if (b == 0x0) {
          // Sync!
          buffer_idx_ = 0;
        }
      } else {
        buf_[buffer_idx_] = b;
        if (b == 0x0) {
          dispatchMessage();
          buffer_idx_ = 0;
        } else {
          ++buffer_idx_;
          if (buffer_idx_ >= sizeof(buf_)) {
            redLED(HIGH);
            buffer_idx_ = -1;
          }
        }
      }
    }

    unsigned long now = millis();
    if (next_time_ == 0) {
      next_time_ = now + 100;
    } else if (now >= next_time_) {
      next_time_ = now + 100;

      // Send update to the driving computer @ 10 Hz with the autonomous status.
      rover12_comm::EstopMsg msg;
      msg.data.autonomous = autonomous_mode;
      msg.encode();
      Serial.write(reinterpret_cast<uint8_t*>(&msg), sizeof(msg));
    }
  }

private:
  void dispatchMessage() {
    int8_t type = static_cast<int8_t>(buf_[0]);
    switch (static_cast<rover12_comm::MsgType>(type)) {
      case rover12_comm::MsgType::ESTOP: {
        auto ptr = reinterpret_cast<rover12_comm::EstopMsg*>(buf_);
        ptr->decode();
        estopMessage(*ptr);
      } break;

      case rover12_comm::MsgType::CONTROL: {
        auto ptr = reinterpret_cast<rover12_comm::ControlMsg*>(buf_);
        ptr->decode();
        controlMessage(*ptr);
      } break;

      default:
        redLED(HIGH);
        break;
    }
  }

  void estopMessage(const rover12_comm::EstopMsg& msg) {
    estop_ = msg.data.autonomous;
    last_estop_time_ = millis();
  }

  void controlMessage(const rover12_comm::ControlMsg& msg) {
    steering_us_ = msg.data.steering_us;
    throttle_us_ = msg.data.throttle_us;
  }

  // Buffer for serial communication.
  uint8_t buf_[100];
  int buffer_idx_;

  // Steering and throttle servo durations (in microseconds).
  int steering_us_;
  int throttle_us_;

  // True = software is requesting autonomous mode.
  bool estop_;

  // Last time we saw an estop message (of any kind).
  unsigned long last_estop_time_;

  // Next time we should send an autonomous mode status update.
  unsigned long next_time_;
};

// Global variables.
WheelEncoders wheel_encoders(100); // 10 Hz report rate
Messenger messenger; // Communication with driving computer.
Servo steering_servo;
Servo throttle_servo;

void setup() {
  // Initialize LEDs.
  orangeLED(LOW);
  redLED(LOW);

  // Initialize wheel encoder pins.
  FastGPIO::Pin<RR_A>::setInput();
  FastGPIO::Pin<RR_B>::setInput();
  FastGPIO::Pin<RL_A>::setInput();
  FastGPIO::Pin<RL_B>::setInput();

  // Initialize estop I/Os.
  FastGPIO::Pin<ESTOP_IN>::setInput();
  FastGPIO::Pin<AUTONOMOUS_OUT>::setOutputLow();

  // Initialize serial messenger.
  messenger.setup();

  // Hook up encoder interrupts.
  attachInterrupt(digitalPinToInterrupt(RL_A), handleRLA, CHANGE);
  attachInterrupt(digitalPinToInterrupt(RL_B), handleRLB, CHANGE);
  attachInterrupt(digitalPinToInterrupt(RR_A), handleRRA, CHANGE);
  attachInterrupt(digitalPinToInterrupt(RR_B), handleRRB, CHANGE);

  // Attach to steering/throttle servos.
  steering_servo.attach(STEER_OUT);
  throttle_servo.attach(THROT_OUT);
}

void loop() {
  // Are we actually in autonomous mode? We only are if both the software and the
  // physical switch agree that we are.
  bool autonomous_mode = !FastGPIO::Pin<ESTOP_IN>::isInputHigh() && // active low
                         messenger.estop() &&
                         messenger.last_estop_time() > (millis() - 500);
  FastGPIO::Pin<AUTONOMOUS_OUT>::setOutput(autonomous_mode);

  wheel_encoders.process();
  messenger.process(autonomous_mode);

  // Set steering and throttle commands.
  if (autonomous_mode) {
    steering_servo.writeMicroseconds(messenger.steering_us());
    throttle_servo.writeMicroseconds(messenger.throttle_us());
  } else {
    steering_servo.writeMicroseconds(1556);
    throttle_servo.writeMicroseconds(1500);
  }
}

void handleRLA() {
  if (FastGPIO::Pin<RL_A>::isInputHigh()) {    // A changed from low to high
    if (!FastGPIO::Pin<RL_B>::isInputHigh()) { // B is low
      wheel_encoders.decrementRearLeft();      //   CCW
    } else {                                   // B is high
      wheel_encoders.incrementRearLeft();      //   CW
    }
  } else {                                      // A changed from high to low
    if (!FastGPIO::Pin<RL_B>::isInputHigh()) { // B is low
      wheel_encoders.incrementRearLeft();      //   CW
    } else {                                   // B is high
      wheel_encoders.decrementRearLeft();      //   CCW
    }
  }
}

void handleRLB() {
  if (FastGPIO::Pin<RL_B>::isInputHigh()) {     // B changed from low to high
    if (!FastGPIO::Pin<RL_A>::isInputHigh()) {  // A is low
      wheel_encoders.incrementRearLeft();       //   CW
    } else {                                    // A is high
      wheel_encoders.decrementRearLeft();       //   CCW
    }
  } else {                                      // B changed from high to low
    if (!FastGPIO::Pin<RL_A>::isInputHigh()) {  // A is low
      wheel_encoders.decrementRearLeft();       //   CCW
    } else {                                    // A is high
      wheel_encoders.incrementRearLeft();       //   CW
    }
  }
}

void handleRRA() {
  if (FastGPIO::Pin<RR_A>::isInputHigh()) {    // A changed from low to high
    if (!FastGPIO::Pin<RR_B>::isInputHigh()) { // B is low
      wheel_encoders.decrementRearRight();     //   CCW
    } else {                                   // B is high
      wheel_encoders.incrementRearRight();     //   CW
    }
  } else {                                     // A changed from high to low
    if (!FastGPIO::Pin<RR_B>::isInputHigh()) { // B is low
      wheel_encoders.incrementRearRight();     // CW
    } else {                                   // B is high
      wheel_encoders.decrementRearRight();     //   CCW
    }
  }
}

void handleRRB() {
  if (FastGPIO::Pin<RR_B>::isInputHigh()) {    // B changed from low to high
    if (!FastGPIO::Pin<RR_A>::isInputHigh()) { // A is low
      wheel_encoders.incrementRearRight();     //   CW
    } else {                                   // A is high
      wheel_encoders.decrementRearRight();     //   CCW
    }
  } else {                                     // B changed from high to low
    if (!FastGPIO::Pin<RR_A>::isInputHigh()) { // A is low
      wheel_encoders.decrementRearRight();     //   CCW
    } else {                                   // A is high
      wheel_encoders.incrementRearRight();     //   CW
    }
  }
}

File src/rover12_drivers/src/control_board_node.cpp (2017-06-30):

#include <cmath>
#include <cstdlib>
#include <string>

#include <ros/ros.h>

#include <geometry_msgs/Vector3.h>
#include <geometry_msgs/Twist.h>
#include <geometry_msgs/TwistWithCovariance.h>
#include <geometry_msgs/TwistWithCovarianceStamped.h>
#include <rover12_comm/rover12_comm.h>
#include <rover12_drivers/AutonomousMode.h>
#include <rover12_drivers/EncoderStatus.h>
#include <rover12_drivers/ServoControl.h>
#include <rover12_drivers/messenger.h>

class ControlSubscriber {
public:
  ControlSubscriber(ros::NodeHandle& nh, rover12_drivers::Messenger& messenger)
    : nh_(nh), messenger_(messenger) {
    ctrl_sub_ = nh_.subscribe("/control/command", 1, &ControlSubscriber::controlCallback, this);
    auto_sub_ = nh_.subscribe("/control/autonomous", 1, &ControlSubscriber::autonomousCallback, this);
  }

  void controlCallback(const rover12_drivers::ServoControl::ConstPtr& msg) {
    rover12_comm::ControlMsg control_msg;
    control_msg.data.steering_us = msg->steering_us;
    control_msg.data.throttle_us = msg->throttle_us;
    messenger_.send(control_msg);
  }

  void autonomousCallback(const rover12_drivers::AutonomousMode::ConstPtr& msg) {
    rover12_comm::EstopMsg estop_msg;
    estop_msg.data.autonomous = msg->autonomous;
    messenger_.send(estop_msg);
  }

private:
  ros::NodeHandle& nh_;
  rover12_drivers::Messenger& messenger_;
  ros::Subscriber ctrl_sub_;
  ros::Subscriber auto_sub_;
};

class EncoderPublisher {
public:
  explicit EncoderPublisher(ros::NodeHandle& nh)
    : nh_(nh),
      ticks_initialized_(false) {
    odom_pub_ = nh_.advertise<geometry_msgs::TwistWithCovarianceStamped>("/wheels/data", 1);
    encoder_pub_ = nh_.advertise<rover12_drivers::EncoderStatus>("/wheels/status", 1);
    estop_pub_ = nh_.advertise<rover12_drivers::AutonomousMode>("/estop", 1);

    geometry_msgs::TwistWithCovariance twist_cov_msg;

    // Covariance is 6x6: x, y, z, rx, ry, rz
    // Diagonal: 0.001, 0.001, -1, -1, -1, -1
    const double x_cov = 0.001;
    const double y_cov = 0.001;
    const double z_cov = -1.0;
    const double rx_cov = -1.0;
    const double ry_cov = -1.0;
    const double rz_cov = -1.0;
    twist_cov_msg.covariance[0] = x_cov;
    twist_cov_msg.covariance[1] = 0.0;
    twist_cov_msg.covariance[2] = 0.0;
    twist_cov_msg.covariance[3] = 0.0;
    twist_cov_msg.covariance[4] = 0.0;
    twist_cov_msg.covariance[5] = 0.0;
    twist_cov_msg.covariance[6] = 0.0;
    twist_cov_msg.covariance[7] = y_cov;
    twist_cov_msg.covariance[8] = 0.0;
    twist_cov_msg.covariance[9] = 0.0;
    twist_cov_msg.covariance[10] = 0.0;
    twist_cov_msg.covariance[11] = 0.0;
    twist_cov_msg.covariance[12] = 0.0;
    twist_cov_msg.covariance[13] = 0.0;
    twist_cov_msg.covariance[14] = z_cov;
    twist_cov_msg.covariance[15] = 0.0;
    twist_cov_msg.covariance[16] = 0.0;
    twist_cov_msg.covariance[17] = 0.0;
    twist_cov_msg.covariance[18] = 0.0;
    twist_cov_msg.covariance[19] = 0.0;
    twist_cov_msg.covariance[20] = 0.0;
    twist_cov_msg.covariance[21] = rx_cov;
    twist_cov_msg.covariance[22] = 0.0;
    twist_cov_msg.covariance[23] = 0.0;
    twist_cov_msg.covariance[24] = 0.0;
    twist_cov_msg.covariance[25] = 0.0;
    twist_cov_msg.covariance[26] = 0.0;
    twist_cov_msg.covariance[27] = 0.0;
    twist_cov_msg.covariance[28] = ry_cov;
    twist_cov_msg.covariance[29] = 0.0;
    twist_cov_msg.covariance[30] = 0.0;
    twist_cov_msg.covariance[31] = 0.0;
    twist_cov_msg.covariance[32] = 0.0;
    twist_cov_msg.covariance[33] = 0.0;
    twist_cov_msg.covariance[34] = 0.0;
    twist_cov_msg.covariance[35] = rz_cov;

    geometry_msgs::Twist twist_msg;

    geometry_msgs::Vector3 linear_msg;
    linear_msg.x = 0.0;
    linear_msg.y = 0.0;
    linear_msg.z = 0.0;

    geometry_msgs::Vector3 angular_msg;
    angular_msg.x = 0.0;
    angular_msg.y = 0.0;
    angular_msg.z = 0.0;

    twist_msg.linear = linear_msg;
    twist_msg.angular = angular_msg;

    twist_cov_msg.twist = twist_msg;

    speed_msg_.twist = twist_cov_msg;
  }

  void wheelEncCallback(const rover12_comm::WheelEncMsg& msg) {
    // Don't publish on first message, just initialize our ticks.
    if (!ticks_initialized_) {
      prev_ticks_ = msg.data;
      ticks_initialized_ = true;
      return;
    }

    // Compute instananeous velocity on each wheel based on previous tick
    // count.
    const int32_t rl_tick_delta = msg.data.count_rear_left - prev_ticks_.count_rear_left;
    const int32_t rr_tick_delta = msg.data.count_rear_right - prev_ticks_.count_rear_right;

    // TODO: Make these params (everything in meters).
    const double wheel_diameter = 0.102;
    const int num_stripes = 20.0;
    const double wheel_circumference = wheel_diameter * M_PI;
    const double meters_per_tick = wheel_circumference / (4.0 * num_stripes);

    // Translate tick counts to distances traveled.
    const double rl_distance = rl_tick_delta * meters_per_tick;
    const double rr_distance = rr_tick_delta * meters_per_tick;

    // Compute time delta based on difference in hardware timestamp.
    const uint32_t hw_timestamp_delta_ms = msg.data.hw_timestamp_ms - prev_ticks_.hw_timestamp_ms;
    const double time_delta = static_cast<double>(hw_timestamp_delta_ms) / 1000.0;
    const double rl_speed = rl_distance / time_delta;
    const double rr_speed = rr_distance / time_delta;

    // Averaging wheel speeds gives a pretty good estimate of true speed.
    const double avg_speed = (rl_speed + rr_speed) / 2.0;

    // Timestamp and identify reference frame.
    speed_msg_.header.stamp = ros::Time::now();
    speed_msg_.header.frame_id = "base_link";

    // Update instaneous forward speed.
    speed_msg_.twist.twist.linear.x = avg_speed;

    // Publish!
    odom_pub_.publish(speed_msg_);

    // Publish raw encoder ticks.
    rover12_drivers::EncoderStatus encoder_msg;
    encoder_msg.header.stamp = ros::Time::now();
    encoder_msg.header.frame_id = "base_link";
    encoder_msg.hw_timestamp_ms = msg.data.hw_timestamp_ms;
    encoder_msg.count_rear_left = msg.data.count_rear_left;
    encoder_msg.count_rear_right = msg.data.count_rear_right;
    encoder_pub_.publish(encoder_msg);

    // Save current tick counts.
    prev_ticks_ = msg.data;
  }

  void estopCallback(const rover12_comm::EstopMsg& msg) {
    rover12_drivers::AutonomousMode auto_msg;
    auto_msg.header.stamp = ros::Time::now();
    auto_msg.header.frame_id = "base_link";
    auto_msg.autonomous = msg.data.autonomous;
    estop_pub_.publish(auto_msg);
  }

private:
  ros::NodeHandle& nh_;
  ros::Publisher odom_pub_;
  ros::Publisher encoder_pub_;
  ros::Publisher estop_pub_;
  rover12_comm::WheelEnc prev_ticks_;
  geometry_msgs::TwistWithCovarianceStamped speed_msg_;
  bool ticks_initialized_;
};
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

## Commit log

2016-07-12 Fix sample bugs.
2016-07-12 Import laser_proc and urg_node packages. They seem to compile.
    [URG.cfg]
2016-07-19 Adding EAGLE library and empty project for wheel encoder boards.
    [wheel_encoder.sch]
2016-07-20 Added MicroFit 2x2 to library and wheel sensor schematic.
    [wheel_encoder.sch]
2016-07-23 Hardware updates.
    [control_board.sch, wheel_encoder.sch]
2016-07-24 Moar work.
    [control_board.sch]
2016-07-24 More work.
    [control_board.sch]
2016-07-24 Yep, more work.
    [control_board.sch, wheel_encoder.sch]
2016-07-24 Getting close on control board.
    [control_board.sch]
2016-07-24 Getting really close!
    [control_board.sch]
2016-07-25 Control board schematic/BOM done!
    [control_board.sch, wheel_encoder.sch]
2016-07-25 Adding sensor board.
    [sensor_board.sch]
2016-07-25 GPS and IMU symbols.
2016-07-27 Sensor board almost done. Needs extra I/Os broken out.
    [sensor_board.sch]
2016-07-29 Add the rover12_description package.
    Added a URDF to describe the coordinate frames of our robot, with some
    visual models for the body and wheels. The rear and front wheels can
    rotate and the front wheels can steer.
    This also adds some useful launch files for visualizing the URDF and
    loading the robot configuration (launch/rover12.launch).
    The configuration of the joint_state_publisher and
    robot_state_publisher have been broken out into YAML files in the
    config directory. There are 6 topics that joint_state_publisher is
    subscribing to, one for each of the degrees of freedom of the URDF. All
    these topics are under the /joints/ namespace.
    [robot_state_publisher.yaml, rover12.urdf.xacro]
2016-07-30 Added AREF breakout to control board.
    [control_board.sch]
2016-07-30 Finished sensor board schematic.
    [sensor_board.sch]
2016-07-31 Added LiPo cell monitors to sensor board.
    [sensor_board.sch]
2016-07-31 Added power board schematic.
    [power_board.sch]
2016-07-31 All parts for power board.
2016-08-01 Power board nearly done.
    [power_board.sch]
2016-08-01 Done with power board schematic.
    [power_board.sch]
2016-08-01 Fixup notes.
    [control_board.sch, power_board.sch, sensor_board.sch]
2016-08-02 Osh Park design rules and mirrored wheel encoders.
    [wheel_encoder.sch]
2016-08-03 Test fitting parts. Rear wheel encoder mostly done.
    [control_board.brd, power_board.brd, sensor_board.brd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]
2016-08-04 Renaming wheel_encoder to rear_wheel_encoder.
    [rear_wheel_encoder.brd, rear_wheel_encoder.sch]
2016-08-04 Adding front_wheel_encoder as a copy of rear_wheel_encoder.
    [front_wheel_encoder.brd, front_wheel_encoder.sch]
2016-08-04 Front wheel encoder mostly done, fixed schematic error in both encoders.
    [front_wheel_encoder.brd, front_wheel_encoder.sch, rear_wheel_encoder.brd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]
2016-08-04 Front wheel encoder passes OshPark's DRC.
    [front_wheel_encoder.brd]
2016-08-05 Rear wheel encoder done and passes OshPark DRC.
    [rear_wheel_encoder.brd]
2016-08-05 Use vector fonts for board silkscreen.
    [front_wheel_encoder.brd, power_board.brd, rear_wheel_encoder.brd]
2016-08-05 Screw head outlines.
    [front_wheel_encoder.brd, rear_wheel_encoder.brd]
2016-08-08 Power board routed.
    [control_board.brd, control_board.sch, power_board.brd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]
2016-08-08 Minor silk adjustment.
    [power_board.brd]
2016-08-08 More minor silk adjustments.
    [power_board.brd]
2016-08-10 Control board getting close.
    [control_board.brd, control_board.sch]
2016-08-11 Finished routing control board.
    [control_board.brd]
2016-08-11 Fix hole size in control board, placment work on sensor board.
    [control_board.brd, sensor_board.brd]
2016-08-12 Routing work on sensor board.
    [sensor_board.brd]
2016-08-12 Sensor board nearly complete.
    [sensor_board.brd]
2016-08-12 Sensor board routed.
    [sensor_board.brd]
2016-08-13 Minor fixups to sensor board.
    [sensor_board.brd]
2016-08-17 Power board fixes for airwires, thermals, Murata pads.
    [power_board.brd, power_board.sch]
2016-08-17 Added inline resistor for reset monitor and rev 2 silk.
    [power_board.brd, power_board.sch]
2016-08-21 Quadrature encoder pattern generator.
2016-08-21 Sized the encoder strip.
2016-08-22 Fix airwire in front wheel encoder.
    [front_wheel_encoder.brd]
2016-09-10 Getting sensor board firmware up and running.
2016-09-10 More sensor board firmware.
2016-09-11 Reading rear quadrature encoders
2016-09-11 Fixed wheel encoder bug.
    [quadencoders.ino]
2016-09-11 Sensor board nearly done for now.
2016-09-11 Get rover12_comm compiling on both sides of the cable.
2016-09-11 Added steering calibration logic
2016-09-11 Print IMU messages.
2016-09-11 Update IMU message and data rate.
2016-09-11 Seperate IMU calibration into ImuCal message.
2016-09-11 Break IMU data and calibration into two separate messages.
2016-09-11 Increased throttle for steering calibration
2016-09-11 Separate IMU cal message in firmware.
2016-09-12 Maria was right. I was wrong.
    [steer_calib.ino]
2016-09-12 Added messages with wheel encoder counts
2016-09-12 Wheel encoders!
2016-09-12 Publishing wheel encoder data!
2016-09-12 Added a script for mapping steering angle to servo commands
2016-09-13 Updated URDF with GPS and IMU frames.
    [rover12.urdf.xacro]
2016-09-13 Lauch file package and initial sensor covariances.
2016-09-13 Control board node sends control and autonomous message.
2016-09-13 Fix my screw up.
2016-09-13 In case we need to reset the Venus again...
    [sensor_board_test.ino]
2016-09-13 Add navsat_transform and map frame localizer.
2016-09-14 PID gains set from ROS params.
    [throttle_pid_gains.yaml]
2016-09-14 Added PI control loop for velocity
2016-09-14 Send PID gains a couple times to make them stick.
2016-09-14 Velocity impulse tool for PID tuning.
2016-09-14 Build a hacky Path message for the planner/display from Odometry logs.
2016-09-14 Use velocity scaling.
2016-09-24 Firmware fixes and debugging.
    [quadencoders.ino]
2016-09-24 Working on PID velocity control.
    [throttle_pid_gains.yaml]
2016-12-22 Documenting tf2 frames.
2016-12-22 Added joint_state_publisher.
2016-12-22 Information about driver nodes and sensor/control topics.
2017-01-02 Remove upstream packages, no longer needed.
    [URG.cfg]
2017-01-09 Minor firmware compile fix.
    [quadencoders.ino]
2017-01-18 Remove PID gains from control_board_node.
2017-01-18 Add ServoControl message.
2017-01-21 Update control board launch file to remove control gains.
    [throttle_pid_gains.yaml]
2017-02-13 Remove debug messages from control board firmware.
2017-02-13 Don't need the velocity_impulse package anymore.
2017-02-13 Add hardware timestamp to wheel encoders message.
2017-06-30 Update firmware to report wheel encoders at 10 Hz.
